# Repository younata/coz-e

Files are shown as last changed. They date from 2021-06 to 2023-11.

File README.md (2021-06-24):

# [Coz-E Build Log](https://coz-e.rachelbrindle.com)



Build log for an electric canard airplane. Built using the same technology as my [knowledge repo](https://github.com/younata/personal_knowledge).

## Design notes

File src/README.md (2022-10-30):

# Introduction - The Coz-E

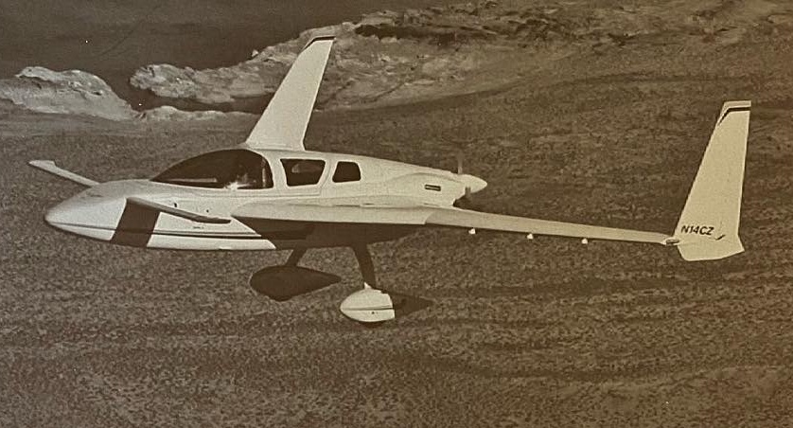
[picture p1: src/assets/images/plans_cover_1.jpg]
Image of the the Cozy Mk IV prototype, from the cover for my copy of the Cozy Plans


This is the build log (and other relevant information) for my cozy-derived electric canard airplane.

You can think of this as a [Cozy Mark IV](https://en.wikipedia.org/wiki/Cozy_MK_IV) with the rear seats replaced with a large battery compartment and an electric motor. Because that's what it will be.

Unlike [my digital garden](https://knowledge.rachelbrindle.com), which provides more generic knowledge and things I've gathered, this site is intended to scope down to the Coz-E.

## Using this site

Pages are organized on the sidebar to the left. It's sorted alphabetically, and most top-level sections have nested subsections. Sections with the chevron next to them can be expanded to show additional subsections. You can also search for things by clicking or tapping on the search icon in the top left.

There is an [rss feed to track updated articles here](/atom.xml). You can also paste any article's URL into your rss reader and it should discover the feed.

## Recent Work

The pages that I've recently been working on.

{{#recently_updated}}

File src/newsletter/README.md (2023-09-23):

# Cozy Newsletter

Marc Zeitlin has <a href="http://www.cozybuilders.org/newsletters/" data-proofer-ignore>all of the Cozy Newsletters available at cozybuilders.org</a>. Here's some of the more relevant information to the Coz-E build.

Note for builders of gas-powered Cozys: I have not included any of the tips related to the fuel and engine systems. This will be a fully-electric airplane, and so I have no reason to include those for my reference.

## Builder Tips

In addition to some of the dedicated articles going in more depth on specific advice, here's a sorted list of most of the advice given in the Cozy Newsletter.

### General

- Keep joints tight with "no joggles" to improve performance. (Cozy Newsletter \#4)
- Do not cut up the large-size drawings. Instead, trace templates onto another sheet of paper and save the original drawings intact. (Cozy Newsletter \#12) (Personally, I take photos of the drawings with a ruler for scale, but that's for archival purposes).
- "NEVER allow yourself to be distracted while working on your airplane, such that you might not complete a task, and then forget to finish it later. We all have had the experience of visitors dropping in while we are working. Even if you have to be rude, finish the job before laying down your tools." (Cozy Newsletter \#24, The Canard Pusher \#57)
- Joints between all permanently installed parts should be taped. (Cozy Newsletter \#24)
- This one comes up in more than a few newsletters: Check your attach bolts. If more than 2 threads extend through the nut, add another washer. Don't let the threads bottom out before the bolts are tight. (Cozy Newsletter \#34)
- Holes through bulkheads or instrument panel do not need to be glassed. (Cozy Newsletter \#36)
- Wherever possible, orient bolts either heads up or heads forward. (Cozy Newsletter \#38)
- "Extruded piano hinges MS20001-P6, P5, P4, etc. are all identical except for the width of the flange. It is easier just to order and stock the P6, and if the flange is wider than necessary, trim it on your band saw."" (Cozy Newsletter \#39)
- Try using a light inside to identify holes that have been glassed over. (Eric Westland, Cozy Newsletter \#39)
- For bending aluminum, rule of thumb is that the bend radius should be no less than the thickness of the material. E.G. 1/16 inch thick aluminum can bend 90°, provided the radius is 1/16 inch or greater. Always bend aluminum across the grain, not with it. (Ray Goldsmith, Cozy Newsletter \#39)
- Always order a little extra material, especially in the beginning, so that you don't run out of epoxy, cloth, micro, or flox before finishing a job. (Cozy Newsletter \#69)
- "all aluminum parts [should] be protected from corrosion by cleaning first with Alumiprep 33 or metal prep \#79, and then soaking in Alodine 1201, which is a visible (golden brown) moisture barrier, greatly increasing resistance to corrosion. This also acts as an excellent surface to bond epoxy or paint. Even if you do not live near the coast, the airplane you are building could some day end up there." (Cozy Newsletter \#81)

### Safety

- Use nitrile gloves for your hand, with water-soluble barrier cream on the arms. Switch out the barrier cream early and often. (Cozy Newsletter \#89)
  - This has evolved significantly, from the original advice, starting way back in \#7: To protect your skin from epoxy, Nat heavily recommends water-soluble barrier creams. If you must use gloves, use nitrile gloves. Under no circumstances, use latex gloves.

### Tools & Shop

- Store and dispense glass cloth on a rack in a wall cabinet. Hinge the front of the cabinet so that it opens to form a table to lay out the cloth for cutting. Keep a clean pair of scissors there just for cutting clean cloth. (Cozy Newsletter \#14)
- Put a 2 inch overhang all around your work table. This makes clamping parts to the table much easier. (Cozy Newsletter \#17)

> Neil Clayton says the tool (s) he uses the most are sanding sticks he made himself. He says Home Depot paint dept gives away 2 sizes of paint stirrers; a 1"wide stick and a 2” wide version. Both have a nicely formed handle. I always grab a handful as I pass towards the check out. Then at Lowe’s I pick up some 12” x 18” sanding sheets (the kind used on those big floor sanders). Several grades are available. I use left over epoxy to glue the stirrers to the sheets and then split them into individual sanding tools with a razor blade when the epoxy has dried. One sheet yields about 10-15 sanding sticks of various sizes so they are cheap and disposable. Try it!

(Cozy Newsletter \#78)

- Get a Fein tool for trimming cured layups and electric scissors for cutting cloth and peel ply (and trimming wet layups) (Cozy Newsletter \#82)

### Antennae

- Make sure the nav antenna misses the area in the bottom of the fuselage that will be cut out later for the nosewheel well. (Eric Westland, Cozy Newsletter \#39)

#### Location

From Cozy Newsletter \#34, with a discussion on where to place the antennas (For a Cozy 3).

- Transponder: In the nose ahead of the rudder pedals with the probe extending through a 1/4" hole in the bottom of the fuselage.
- Nav: Two good locations:
  1. Underneath the skin on the bottom of the canard, legs extending forward and offset to the radio side.
  2. Under the skin on the bottom of the fuselage, legs extending forward on either side of wheel well.
- ADF: Use King electronic antenna and locate inside cockpit under right front seat.
- Com: Located under skin of winglets, per plans.
- FM and/or Marker Beacon: Under skin mid-wing.

GPS was not specifically called out, presumably because it wasn't available back then.

- Be careful in laying out VOR antennas on the bottom of the fuselage to avoid future cut outs for the landing light and nose wheel. (Thomas Kennedy, Cozy Newsletter \#55)

> Here are the dimensions (each arm) Jim Weir has published for the following di-pole antennas:
> - Marker Beacon - 34.3 in.
> - FM Music Radio - 26.2 in.
> - VOR/LOC - 22.8 in.
> - VHF/COM - 20.3 in.
> - Amateur 2m - 17.7 in.
> - Glideslope - 7.5 in.
>
> The COM is the only one that needs to be vertically oriented. All the rest should be horizontal. The VOR should be a V shape. Some say the marker beacon should be along the airplane centerline. I installed mine in the wing and it worked just fine. You should keep the tips of di-pole antennas away from metal, and away from each other, particularly transmitting antennas. I have used Jim's measurements and they work well-better than most factory antennas. My GPS antenna is mounted in the nose, just under the inspection cover (pointed upward toward the satellites) and works well there. I like this location because the co-ax is very short. My transponder antenna is in the bottom of the nose, with the probe just sticking through the skin (pointed down toward the ground stations). You can make your own transponder antenna. It should be 2.65 inches long from the tip of the probe to the ground plane, and insulated from the ground plane. The ground plane can be made from .062 aluminum. It is about 8 inches in diameter (I lost my drawing). I have made my own from one of Jim's kits, and also from scratch, and they work well. You attach the center conductor to the radiating rod, and the co-ax ground to the ground plane. You get a lot of satisfaction when you make your own antennas, they are all hidden, and they work better than the ones that cost mucho bucks!

(Cozy Newsletter \#73)

### Canard

> Several Mark IV builders have advised us that their canards are slightly longer in cross section (chord) then shown on M-11, and when the lift tabs are in contact with the forward face of F-22, the trailing edge of the canard is 1/8 to 1/4" aft of the forward face of F-28, and that the alignment tabs cannot be built as shown. Should this also be the case with your canard, you may lay up additional plies of BID locally on the forward face of F-22 up to 1/8" thick, or remove up to 1/8" of the trailing edge of the canard locally at the tabs, or a combination of both.

(Cozy Newsletter \#44)

> Canard installation. Make sure you allow for at least 3/4" of horizontal travel for the canard so the incidence pins will not bind during installation or removal.

(Cozy Newsletter \#50)

> Some builders are still having trouble with the trailing edge of their canard being too low, such that the airfoil dips down and they have to mount the elevators lower than desired to get the required 15 degrees of trailing edge up travel. We suggest that you remove 1/16th inch (no more) from underneath the fishtail on the templates before cutting the foam cores, or from the foam after cutting to avoid this problem. We have made this suggestion to Feather Lite as well to do on their precut cores.

(Cozy Newsletter \#53)

### Canopy

On getting a smooth edge where the fiberglass contacts the canopy:

> Builder Wayne Hicks said he made a paper pattern of the canopy deck, then laid up the 2 UND on plastic (and later the 2 BID), used the pattern and razor pizza cutter to make a nice, clean cut along the pattern lines. Then he laid the piece nice and neat up against the glass. There were absolutely no problems. No excess flox, no excess resin, no excess glass. Never had to use a dremel! If anything, all he had to do was cut one or two stray strands with a razor blade. He did this for both the outside and inside canopy deck layups, and highly recommends this technique.

(Wayne Hicks, Cozy Newsletter \#70)

> to avoid corrosion of the canopy hinge attach bolts. Saturate the bare wood in the holes through the longeron with epoxy to seal the wood fibers. Do this by dipping a cotton swab into epoxy and then inserting it into the hole. Alternatively, you can drill the hole slightly oversize, fill it with flox, and after cure, redrill it to the correct size.

(Nick Parkyn, Cozy Newsletter \#83)

### Contouring

- Fill low spots before sanding surrounding areas down to contour. This keeps your low spots from turning into high spots. (Cozy Newsletter \#22)

> I found a method to make the final canard contour perfect per plans. I used the checking contour templates for the canard to cut out (hot wire) a block of styrofoam. Then I stuck a large piece of sandpaper to it and used it to give the canard a perfect contour over its entire length. The same thing worked fine for the elevators.

(Jean-Jacques Claus, Cozy Newsletter \#85)

### Cowlings

> Cowlings should have extra layers of BID along all the edges to make them more rigid when they are removed from the airplane, and to provide more beef for the fasteners. This is shown in Figures 12 & 15, Chapter 23, but builders were not instructed to add them because the supplier (Featherlite) added them while the cowlings were still in the mold. In February 1999, when we inspected AeroCad cowlings, we noticed that they were not doing this. We asked them to add the extra layers while the cowlings were still in the mold. They agreed, and we approved their cowlings contingent upon their doing this.

(Cozy Newsletter \#68)

### Elevators

> Your elevators should balance with the weights shown in the plans. If they do not, do not try to balance them by adding weight inboard. Instead, discard them and make new ones more carefully to make them lighter (you can probably re-use the torque tubes and other hardware). The mass balance called out for the elevator and the specification for balancing them applies only to an elevator fabricated with the same weight and stiffness as that which has successfully passed all the flutter testing. It is extremely important, and life-critical that the manufacturer or owner of each Cozy, or any plane for that matter, assure himself without a doubt, that the control surfaces are conformal to those which have passed flight tests and been shown to be flutter-free.

(Cozy Newsletter \#24)

> Elevator torque tube offsets (CZNC-12A for the Roncz canard). The drawing we submitted to Brock Mfg. stated that these offsets should be a slip-fit in the l" OD x .035" 2024 T3 torque tube. Brock Mfg. cannot guarantee a slip-fit because the tolerance on wall thickness for .035" 2024 T3 drawn tubing is +/-10 %. To prevent too loose a fit if the wall thickness is on the thin side, the specification for the offsets has been tightened to .930' OD. If the wall is on the thick side, you will have to sand the offsets to obtain it slip-fit.

(Cozy Newsletter \#50)

> In the first edition Mark IV plans Chapter 11, p.7, we instructed builders to mount their elevators at zero degrees with jig L so that there was a .2 inch gap between the canard and the elevator. When some builders did this, they were not able to get 15 degrees trailing edge up of the elevators. So we changed the L jig (see p. M-18) to mount the elevators at 15 degrees trailing edge up and zero gap. Please note this on p. 7, Chapter 11, 1st paragraph and Figs. 17 & 18.

(Cozy Newsletter \#68)

### Epoxy

Starting with Cozy Newsletter \#61, the MGS system is now recommended. Either the L335 or L285 system.

- Save the foam scraps. Many parts can be made by gluing small pieces together with 5-minute epoxy. (Cozy Newsletter \#5)
- To conserve epoxy, mix microballoons with any excess into a very thick paste, and trowel that over your finished fiberglass parts. This will save you time when finishing. Rough the surface with 36 grit sandpaper first, though. (Cozy Newsletter \#5)
- Lava soap works great to remove epoxy from your hands. (Cozy Newsletter \#35)
- Use the bottom of 8 ounce mixing cups to make 5 minute epoxy (Cozy Newsletter \#17)
- Store near-empty bottles of 5 minute epoxy on their side. (Cozy Newsletter \#28)
- Mixing some flox with 5 minute epoxy will make a bit stronger joint and prevent it from running. (Cozy Newsletter \#35)
- Epoxy Resin should be clear and colorless (or a slight yellow). Hazy indicates crystallization, and the epoxy should not be used until it is heated and becomes clear again. (Cozy Newsletter \#85)

> Cozy builder Phillip Johnson, in the Pacific Northwest, protects his resin and hardener from exposure to air by putting a plastic bag over the top of his plastic containers in his dispenser after filling them, with the bag resting on top of the liquid surface and with enough slack so the bag will follow the surface down as material is used, and then putting the cover on the container.

Cozy Newsletter \#54

### Fiberglassing

- Micro joints (which hold urethane blocks together) cause bumps when glass is laid over them. Undercut all joints with a dremel before shaping and before layup. Fill the undercuts with fresh micro just before the layup. (Cozy Newsletter \#5)
- To prevent air bubbles from coming back in after being worked out, cover the cure area with saran wrap (or any plastic wrap) and squeegee the air out. (Cozy Newsletter \#5)
- Cut the glass cloth ahead of the layup to the approximate size. Do this after the foam is vacuumed, but before applying any epoxy. Drape the cloth over the part, cut it to size, label it with a felt-tipped pen, roll it up and set it aside. (Cozy Newsletter \#14)
- To prevent UNI from unraveling when cutting it lengthwise, lay down a strip of masking tape and cut down the tape's center. Scissor trim the masking tape off after the cloth has been wet in place. (Cozy Newsletter \#14)
- Use a sabre saw, not a band saw, to cut fiberglass. (Cozy Newsletter \#17)
- Use a rubber squeegee to spread epoxy on the glass. Take a 6 inch squeegee, and cut it in 2. Remove the epoxy after use. You can use a belt sander to remove any cured epoxy, but it's less work to just clean it. (Cozy Newsletter \#31)
  - It takes a couple of minutes for epoxy to soak in and wet out one or two layers of glass cloth. Rather than waiting for this to happen in a small area, use this time to spread epoxy over as wide an area as possible. Pour a ribbon of epoxy on the cloth and follow behind with the squeegee spreading it. Keep the pressure very light, so as to not disturb the cloth. After the cloth is wet out, you can increase the pressure of the squeegee to distribute it. You can pick up excess epoxy with your squeegee, wiping it off on the edge of your mixing cup. Conversely, you can apply a small amount of epoxy by dipping your squeegee into the mixing cup. If you practice these techniques, you will find that you can make lay ups much more quickly.
  - Do not waste time trying to get just the right amount of epoxy on the lower layers of a multi-ply layup. Actually, cloth wets out better from underneath and not as much air is trapped between layers. It is only on the last layer that you need to spend the time working on getting the air out an applying the optimum amount of epoxy.
  - Do not leave bristles from the throw-away brushes behind in your layups--they weaken it. You can pick them up with the tip of a brush.
- Double check that you remove the peel ply. If you leave it in and glass over it, the part must be discarded and rebuilt. (Cozy Newsletter \#37)
- Instead of peel ply tape, get the 38 inch wide peel ply. Then, when you need tape, cut the peel ply to whatever width you need. (Eric Westland, Cozy Newsletter \#39)
- "Buy cheap 100% polyester (or Nylon) cloth (peel ply) by the bolt and cover all layups with it. First test a sample piece to make sure no additives are present that may cause removal to be difficult. I find that I do not need to add extra resin to wet out the polyester, just stipple and use a hair dryer. I make it a habit to strip the polyester the next day, so none is left by mistake. This eliminates the need for a lot of sanding, and dust breathing. All layups look and feel smoother." (Steve Blank, Cozy Newsletter \#46)
- "We use peel ply extensively on all of our layups. Glass fibers act somewhat like a sponge, and can soak up extra resin. If a layup is resin-rich, it is not only too heavy, but it is weaker than a layup with just the right amount of resin. The peel ply seems to hold the fibers down more compactly, so they don't soak up too much resin. Sort of a poor man's vacuum bagging. If you use peel ply, you can make the layup a little wet, then lay down the peel ply, and with a squeegee and hair dryer, remove the excess epoxy (if the layup was really wet) or else free up almost enough epoxy to wet out the peel ply, and add epoxy as necessary to wet it out completely. The only thing you need to be careful of is that the layup underneath the peel ply isn't so dry that it is porous, because then the compressive strength would suffer (buckling in compression). Synthetic fabrics with a straight weave (not knit), like nylon, polyester, or dacron, as long as they aren't fuzzy, and don't contain cotton or rayon, seem to work well. Sometimes you can find real bargains at fabric stores. But test a swatch first. Alexander Aeroplane lists peel ply at $2.25/yd. in 45" widths, which is quite reasonable." (Cozy Newsletter \#47)
- "BID is always cut on the bias and overlapped l' in every direction, but UND is overlapped only in the direction of the major fibers." (Cozy Newsletter \#50)
- Whenever possible, use peel ply. As an extra precaution, sand the surface that the peel ply was on before applying the bond. (Cozy Newsletter \#55)
- A wet-on-wet layup usually results in the strongest bond between layers. To do this, wet out the first layer of glass, squeegee the air out, but leave an excess of epoxy and then lay down the next layer of cloth on top to soak up the excess. (Cozy Newsletter \#55)
- Do not glass over a cured, microed surface, if structural strength is required. (Cozy Newsletter \#55)
- Put flox in a bag and dispense it like cake frosting. (Dave West, Cozy Newsletter \#62)
- In tight corners where it's hard to roughen up the surface with conventional sandpaper, try a carbide studded grout removal tool that has carbide deposited on the edge of a steel blade approx. 1" long attached to a handle with a slight "S" bent arm. (John Fritz, Cozy Newsletter \#66)

> Early in the game we learned that various fabrics sold in fabric stores work well as peel ply, and can sometimes be purchased at quite a low price. We learned that hard-weave (not fuzzy or stretch weaves) nylon, polyester and dacron work well. Watch out for cotton and rayon. Often there are roll ends tables where things are reduced for clearance. Once I was able to purchase nylon like is used in ski jackets for $.45/yd, and later wished I had bought the entire table. It is best to take a sample home first, use it on a wet layup, and make sure it peels off, before buying a whole bunch. Make sure you iron any wrinkles out of peel ply before using it. Otherwise they transfer to the layup.

(Cozy Newsletter \#68)

- A general rule is that whenever joining two or more intersecting surfaces together, they should always be floxed and taped, whether instructed to do so or not. (Cozy Newsletter \#71)

- - A rule of thumb for estimating how much mixed epoxy you will need for any given layup is 1 oz of epoxy for every oz of cloth needed. This includes the micro layer. "For example, the bottom side of one Cozy MKIV wing will need 12 yards UNI (7 oz/yd. 38” width) or 84 oz. total. Epoxy weighs 9 lbs. (144 oz) per mixed gallon, so you will need 84 oz. mixed epoxy to wet out 12 yards of UNI." (Cozy Newsletter \#80)
- Leave a little mixture of epoxy in the cup and check it for cure the following day. If it has cured correctly, a scratch on the surface will leave a white mark (Cozy Newsletter \#81)
- "[If] glass cloth wets out and becomes transparent, it is safe to use. If it stays white, throw it away." (Gary Hunter, Cozy Newsletter \#83)
- "DO NOT USE glass that has become wet." (Gary Hunter, Cozy Newsletter \#83)
- Take your time. Do not apply epoxy until you are 100% satisfied with the shape and integrity of the part. (Neal Johnson, Cozy Newsletter \#84)

#### Tom McNeilly's Vacuum-bagging technique

From the Cozy Newsletter \#4, this describes a way to get very light layups using vacuum bagging. Later newsletters state that vacuum-bagging is generally not worth the effort, though.

> Place the layup down as quickly as you can, cover it with perforated poly. Cover that with soft carpet underlayment foam, and cover that with regular poly. Tape down the edges, and pull a vacuum with a vacuum cleaner house between the layers. The vacuum should squeeze the excess epoxy out of the layup and into the soft foam. After cure, strip the coverings off, including epoxy. Tom claims this saved 6 lbs per wing.

#### Dealing with BID

- You can create 2 inch wide BID cloth tape by rolling the BID cloth into 1 inch diameter rolls at 45° to the selvage edge. (Cozy Newsletter \#4)
- For installing BID into the corner tapes: Layup the BID you'll need onto the foil. Squeegee it out to a good layup. Cut your tapes out of this layup, cutting through the glass and aluminum foil. Sand and paint a coat of epoxy onto the area to be laid up over, then use your fingers to bend the aluminum foil to form the tape into an angle to fit into the corner. Position it, then lightly squeegee or stipple it into place. Peel the aluminum foil off, stipple any remaining air bubbles out, peel ply the edges. (Cozy Newsletter \#4)
- Sand a slight recess (1/32 inch) into the foam on flat or curved surfaces where you'll place BID overlap joints so overlaps won't cause a bump in the finished surface. (Cozy Newsletter \#5)

### Finishing

- Don't use featherfill. It does not bond well with epoxy and will cause the paint job to delaminate in a year or two. (Cozy Newsletter \#10)
- Make sure to fill and finish paint the inside of the cowlings. (Cozy Newsletter \#22)
- Most silicones give off corrosive fumes, Dow Corning Silastic RTV 738 is a non-corrosive sealant, use it to secure the cover plates over the wing attach bolts. (Bruce Ibbotson, Cozy Newsletter \#22)
- Use Polyurethanes, not Enamels or Lacquers. Enamels and lacquers chip in heavy rain. (Vance Atkinson, Cozy Newsletter \#23)
- "It is not necessary to use a spray booth to paint an airplane and get a good finish. You can spray the finish coat in a garage or outside. After cure, wet sand with 1000 and then 1500 grit, and then buff with 3M Finess-it II. This will remove orange peel, overspray, dust, and other imperfections and result in a very flat surface with high sheen. This works well with Ditzler Deltron (acrylic urethane) which is the finish we recommend." (Cozy Newsletter \#41)
- "We recommend use of a high-build epoxy primer. Cozy builder Nick Parkyn in Western Australia says that he has used the new System Three water reducible Epoxy Primer and
Polyurethane paints and is impressed with the performance. We are not familiar with these products and have asked him for more information. We would welcome other builders input." (Cozy Newsletter \#41)
- "Have you ever tried to pour paint from a full 1 gallon can and had it run down the side? Try this. Wrap a strip of masking tape (2- wide works the best) around the top of the can, and punch a hole in the groove around the rim. You should be able to pour without spilling, and the excess paint should drain through the hole back into the can. The hole will be sealed after the cover is reinstalled." (Cozy Newsletter \#41)

> Mark IV builder Chuck Larson writes, "I've discovered a tip that works great for wet sanding the Sterling primer. I use a grouting trowel which is used for grouting ceramic tile. I bought mine years ago at Color Tile. It is 9" x 4". It has a wooden handle attached to an aluminum plate which has dense rubber foam bonded to it. Wet or dry sandpaper will adhere to the foam rubber well enough to allow the sanding. It keeps the surface flat, and it is easy to remove and wash out the sandpaper".

(Cozy Newsletter \#44)

> If you need to pour paint from a can without spilling and wasting a lot (paint is expensive!), first punch a hole in the trough around the rim to let paint drain back into the can. Then wrap some 2" tape around the rim of the can, extending up above the rim about 1-1/2". Now you can pour the paint out of the can without it running down the side of the can, and any excess will drain back into the can.

(Cozy Newsletter \#45)

- If you use masking tape when painting, don't leave it on a long time, and when you remove it, pull it back at 180° to itself, not 90°. (Cozy Newsletter \#63)

>
I just completed painting the bottom of my plane. I've used the new poly fiber system. All water based. Very impressed. Pin holes are a total non-issue. Particularly when you use the Superfil instead of normal microballoons. Superfil is substantially better than micro. Trapped voids are rare. Sands easy, mixes easy. Areas where I used micro have more pinholes, but using the Smoothprime primer is highly effective at filling pinholes. It really does flow into holes. Must have low surface tension or something. I also elected to use their water based "topgloss" top coat (polyurethane). So far, I really like it, but I have yet to color sand and buff the paint, so the verdict is still out. I haven't done adhesion tests yet. On my second coat (of three) of topgloss, I got too aggressive and had quite a few runs on corner radius. I elected to sand the entire coat before applying my last coat. Final coat looks good, although areas have a matte appearance (too lean). No runs. The top coat appearance is quite sensitive to spray quantity. More is better unless you develop runs. I had no problems with vertical surfaces. I learned that I don't need to use finer than 120 grit when sanding micro or superfil. The primer fills all those scratches fully. I used a sanding stick only to achieve straightness, then I used an electric random orbit sander with 220 grit. I was willing to sand the primer completely off to achieve uniform appearance. I mixed paint and primers 1 cup at a time to avoid splatter. I've heard people describe sanding and painting as the worst part of the process, but I enjoy it. It's great to see objects finally transformed into airplane like appearance. Just wanted you to know more about these new products. My superficial conclusions: Superfil micro replacement is way better. Smoothprime primer is way better. Topgloss top coat may not be better (lotta work)....we'll see when I'm further along.

(Al Wick, Cozy Newsletter \#67)

> I put the drip lip on the front fuselage cover last night. Here is a hint for those who have yet to do this. The plans say to build up an 1/8 inch ledge with balsa or foam. I used a piece of 1" wide webbing (either climbing rope type webbing or load binding strap type webbing) with duct tape on top of it. The webbing will bend around the curve just right, and it is about the right size.

(Norm Muzzy, Cozy Newsletter \#72)

- Do not use polyurethane paint. Nat recommends a acrylic-urethane (PPG "Deltron" or "Concept") (Cozy Newsletter \#83)

### Fuselage

- If you have difficulty stickling the copper foil tape to the bottom of the fuselage, try heating it with a hair dryer and pressing down on it with a hard rubber roller. (Eric Westland, Cozy Newsletter \#39)

#### Fuselage Sides

- Put a 6" wide strip of wax paper between the masonite and the foam pieces where the edges butt together. This will make the eventual removal from the jigs MUCH easier. (Thomas Kennedy, Cozy Newsletter \#49)
- In assembling the bulkheads to the sides, forget the ropes to tighten the whole assembly. Use threaded rods and wing much more precise control. (Thomas Kennedy, Cozy Newsletter \#49)
- Buy a kiln-dried board (not construction grade) for your WL 0.0, and use bolts rather than nails to secure. This will allow precise placement and later shimming if required. (Thomas Kennedy, Cozy Newsletter \#49)
- I had very good results mounting my WL 0.0 board on my work table which was mounted to 4x4s glued to my garage floor. There is no such thing as a level garage floor. The work table becomes your level surface. (Thomas Kennedy, Cozy Newsletter \#49)

### Foam

- Before cutting wing sections, clamp the styrofoam blocks and glue them using pour foam. This produces very thin joints that keep the styrofoam joined together while still allowing the hot wire to cut them without catching. (Tom McNeilly, Cozy Newsletter \#4)
- You can use a dremel tool with a router attachment to make the small depressions in foam as called out in the plans. (Cozy Newsletter \#15)
- Covering the edges of hot wire templates with copper foil tape makes them easier to use (Cozy Newsletter \#38)
- "The 2 lb./cu.ft. large cell blue styrofoam called for in the plans is called Styrofoam in the Aircraft Spruce catalog, Polystyrene in the Wicks catalog, and extruded Polystyrene in the Alexander catalog. Urethane foam may also be called Polyurethane foam." (Cozy Newsletter \#39)
- Use a router to carve 1/8 inch and 1/16 inch relief cuts in the foam (e.g. in chapter 9, on the landing brake). Attach the router base to a 36 inch long board to make quick, smooth work of the cuts. (Eric Westland, Cozy Newsletter \#39)
- Try using double-sided tape on the forms to hold the foam down. Recommended the kind used on golf club grips or carpet tape. Should peel right off with little or no effect on the foam. (Mark Loy, Cozy Newsletter \#64)

> If you “screw-up” when cutting airfoils, and have a bad cut on one side (top or bottom), no need to throw it away and start over. Just slice the airfoil apart, and splice in a piece of styrofoam (like making a sandwich), and re-cut it. Don’t know how to make a sheet of styrofoam? Just clamp your hotwire saw 1⁄2 inch or so above your work bench, and slide your scrap chunks of styrofoam underneath, sorta like cutting boards from logs. The beauty of composite construction is its hard to spoil something so bad you can’t fix it.

(Cozy Newsletter \#77)

### Joints

> For Structural reasons, all joints should be taped with 2 plies of BID 2' wide (1" on each surface) cut on the bias (45 degrees) unless otherwise specified. After application, the tape should be peel-plied. One recommended way to accomplish this is to wet out 2 plies of BID on wax paper or Saran wrap, cut into strips, apply over joints, remove the wax paper or Saran wrap, cover with peel ply and wet out same. Wax paper should only be used with discretion. It should not be left in place while the epoxy cures, because wax will be left behind, and it should only be used on those joints which will not be later covered with additional layups.

(Cozy Newsletter \#50)

### Landing Gear

- "If you wrap the gear leg first with 1/8" fiberfrax, and then with shiny aluminum, you will greatly reduce the heating by radiation." (Cozy Newsletter \#24)
- "Provide a vent for hot air to escape from your wheel pants. Hot air rises and will be trapped inside the wheel pants unless you provide a vent, on the top, on the disc side, for it to escape." (Cozy Newsletter \#24)

> In Chapter 9, p.2, it says that the [landing gear] strut should be cut at 8 degrees, but on p.3 it says 13 degrees. There has been some disagreement as to what is the correct angle, and it also depends on whether it is measured at the leading edge or trailing edge. The angle is not critical, so shoot for somewhere in between.

(Cozy Newsletter \#68)

> I thought it was in the plans, but maybe not. An easy way to make the fairing where the main gear strut enters the fuselage is to shape it with molding clay (Playdough), glass over with at least 2 layers of BID, attaching to both the strut and the fuselage. Then after cure, make a saw cut at least 1/8" wide halfway between the fuselage and strut, remove the strut, and dig out the clay. If the cut is wide enough and the inside of the fairing is empty, the strut can flex without cracking the fairing. This should be done when the fuselage is upside down with no weight on the gear. Then when you are flying, both halves of the fairing will be aligned for minimum drag.

(Cozy Newsletter \#72)

### Panel

- Don't cut holes for your panel until everything else is done, and you've put together the instrumentation. Build a mock panel first (Nat suggested 1/4 inch plywood. You can also use cardboard) to test it out. (Cozy Newsletter \#5)

### Spars

> The 3 inch spar cap material presently being supplied is only 2-3/4 inches wide, but not to worry. If you pull out the cross threads as instructed for the canard, centerspar, and wings, and then squeegee after applying epoxy, the strands spread out to 3 inches, and you will be able to fill up the troughs with the maximum amount of glass they can hold.

(Cozy Newsletter \#65)

### Strakes

> Bending 3/8 in. PVC is a universal problem. When I re-built my right strake, I made a scribing tool from a block of wood and a hacksaw blade. I made a saw cut in the wood and 5-minuted in the hacksaw blade so it protruded 1/4 in. I carefully scribed a number of cuts in the PVC where I wanted it to bend, then bent it into the frame and fastened it in the bent shape, and then microed and glassed the scribed surface. That worked better than anything else I have tried to date.

(Cozy Newsletter \#10)

- Postpone installing the center section spar and building the strakes until you have completed as much work inside the fuselage as possible. It is much easier to work inside the fuselage with it sitting on its side on saw horses. (Cozy Newsletter \#35)

> It is important for appearance that the strakes are straight (no bumps), and properly aligned with the wing. The wing should be installed on the center section spar when the strake is built, and a straight edge should be used to make sure that the leading edges of the ribs are aligned with the leading edge of the wing, and that all points on the rib airfoils align with the wing airfoil. Of course, you will need to make allowance (using spacers) for the 3/8" foam and several layers of glass skin which will be subsequently be laid over the ribs.

(Cozy Newsletter \#44)

> Strakes, Chapter 21, p.2. Please note that the fuel cell ends at Rib R-57. The empty space outboard is necessary as a buffer to prevent any fuel, liquid or vapors, from reaching the wing. An open drain at the low point would indicate any fuel leakage through R-57.

(Cozy Newsletter \#64)

> Keith Scull (England) didn't want to pay the cost of shipping Featherlite's leading edges all the way from California, and he didn't like the idea of carving foam blocks, so he came up with an innovative alternative. He purchased some thin card stock from a local art supply store, wrapped it around the leading edge of the strake using the ribs as guides, trimmed it so it just fit into the recess provided for the leading edge layup, and taped it in place with 20 inch long strips of masking tape. Then he cut openings in the top so he could pour pour-foam into the empty space. The openings were 3 in. x 1/2 in. every 6 to 9 inches parallel to the strake leading edge. He poured the pour foam thru the slots, let it expand and cure, and then removed the masking tape and card stock. He said the result was a perfectly formed leading edge which required very little sanding to prepare if for the glass layup (see pictures). He said it sounds like a lot of work, but only took a couple of hours, and did a better job with less mess.

> Keith said when he leak tested his strakes using an altimeter, the right strake had a very small leak (20 ft. in 3 hrs.). He couldn't find it with soapy water. So he called in a local refrigeration man who filled the strake with R22 and used an electronic sniffer to locate the escaping gas. He found the leak. It was traveling along the score lines he had cut in the foam to bend it around the ribs, and escaping where the foam joined the fuselage. Apparently he hadn't completely filled up these score lines with micro. The cure was quite simple. He drilled a very small hole thru the top skin into the score line at the tank rib and injected epoxy using the vacuum method described in the plans. To be doubly sure, he did this with every one of the score marks, and found three to be leaking. After filling with epoxy, the altimeter indicated no more leaks.

(Cozy Newsletter \#68)

### Wings

> There is a discontinuity (dip) in the top surface of the wing at B.L. 67.5 (see Chap. 19, p. 10). This is intentional. You have not made a mistake!

(Cozy Newsletter \#53)

> when you attach the wings many times in the shop, don't use the
AN365 nuts over and over again, but instead get some fine thread nuts at the hardware store which are much easier to install and you don't have to worry about them wearing out.

(John Epplin, Cozy Newsletter \#73)

### Unsorted

#### Jim White's advice

From Cozy Newsletter \#67, copied verbatim:

1. Attach the wing before working on the stake and bondo a 1/4" or so thick template to the end of the main spar that matches the contour of the wing. This is needed so that the strake matches up to the leading edge.
2. When cutting out the top and bottom PVC foam pieces, finish one (top or bottom). The top is the same as the bottom except it is 0.2" longer. All the angles are the same. Use the top or bottom strake as a template by simply shifting it up or down 0.2" accordingly. You might as well make all four top and bottom skins at once. GET THE FIRST ON RIGHT, OR YOU WILL HAVE 4 WRONG ONES.
3. I placed blocks under the ends of the landing gear struts to level the airplane perfectly and give it a solid foundation. I supported the jig table with two saw horses, and four pieces of 2x4's individually clamped to the saw horses. The jig table simply rests on the ends of the 2x4's that are adjusted up or down.
4. INSTALL THE RELEASE TAPE ON THE BACK OF THE JIG TABLE BEFORE ATTACHING IT TO THE MAIN SPAR.
5. Use long clamps from the top of the spar to the jig table beneath to firmly attach the plane to the jig table, inboard and outboard on the spar. I did not use any bondo and the jig table never moved relative to the plane, even when getting in and out of it repeatedly to cut out the openings and tape the inside joints.
6. I believe the strainer inspection hole in B33 is marked wrong in the plans. The inspection hole should start 6" from the spar, not 3".
7. For B33 bulkhead reference I clamped a straight edge to the canard bulkhead and strung a string back to a mark on the top of the spar. For the B57 bulkhead I simply used a plumb bob hung over the edge of the jig table at BL 57 and attached the other end to a mark at 57" from centerline on the spar.
8. The B.L. dimensions are to the INBOARD face of the bulkhead. Carve the outboard to get the contours of the bulkheads to match the sweep of the strake. DO NOT CARVE THE INSIDE EDGES.
9. String a line from the leading edge of the template you made in step 1 above to the fuselage using the leading edge of the bulkheads as a guide. This will ensure the leading edges of the wing and strake come together.
10. 1 inch spacing is fine for the scoring of the bottom foam to bend around the ribs.
11. On the top foam, 1/2 inch cuts minimize the flat spots which occur on the top of the
curved part of the strake between the two bulkheads. Make the cuts just after the 1 ply layup has cured. If you can make the cuts while the fiberglass is hard but still pliable, you can bend it over the ribs and let it finally cure in its final shape.
12. I fully trimmed the strake openings into the fuselage before putting the top on permanently. If you jig the top foam sufficiently, it will match up repeatedly to the same place on the fuselage.
13. I wanted to make sure my upper skin was firmly attached to the ribs so I made a flange to go on the bulkheads instead of simply stacking flox on the bulheads. The flox method probably works just fine, but I have heard of some Cozys developing fuel leaks after time and thought this might minimize the possibility of this occurring. This modification added several days work to the process! When the top foam is all ready to flox to the bulkheads, I carefully marked the location of the bulkheads on the bottom of the top strake skin. I then turned the top foam over. You only need to do this for the interior fuel tank edges. Do not extend the flanges into the storage area. You can tape those areas like normal. Do the leading edge, but not the trailing edge along the main spar. On top of each bulkhead marking I put a wide layer of box sealing tape, followed by a layer of peel ply, one layer of bid tape 2" wide, and peel ply on the outer edges of the 2" bid tape. On this second layer of peel ply, DO NOT PUT THE PEEL PLY WHERE THE BULKHEAD OR RIB WILL SIT. Err on the cautious side when putting on this peel ply. You can always sand the area not peel plied, but it is difficult to remove peel ply between the flange and bulkhead. Place a thin layer of flox on the bulkheads and place the top on to cure. Let it fully cure for at least a day or the one layer of bid will sag after you pull the top back off. Pop the top off and remove all the peel ply. Glass the interior corner of the new flange with one layer of bid tape, let cure, trim with dremel, and "voila", flanges that perfectly match your strake skin.
14. When you place the top skin to the bulkheads and ribs, realize that it is a ton of work to tape all the inside edges. But doing the top skin placement and inside tapes in one sitting will save lots of sanding while upside down in the back of your airplane.

### Owners Manual

#### Updates from Newsletter \#52

From Cozy Newsletter \#52:

Do not fly until you add the following information to the Takeoff performance section of the Owners Manual, and comply:

**High Density Altitude Takeoffs**

The combination of high aircraft gross weight and high density altitude represent significant dangers for takeoff obstacle clearance. Special care is required to avoid premature rotation, i.e., if liftoff is too slow, the aircraft will be on the back side of the power curve and may not climb.
When operating heavy and high (say, within 100 lbs. of gross weight and above 5,000' density altitude) do not fully rotate to liftoff attitude until your airspeed is within 5 kts. of the best rate of climb speed, for your specific weight and altitude (see climb charts). This will require more runway than a slower liftoff, but will assure the best capability to clear obstacles and continue a safe climb. Never attempt takeoff under conditions in which you cannot achieve best rate of climb speed while still on the available runway. If this ability is not clear at any point during takeoff_abort. Off-load weight or wait for a cooler time of day.
Lift-off is possible as slow as the minimum lift-off speed, and can be successfully used at light weights and/or low altitudes to achieve a short ground roll. However, that technique will usually result in inadequate initial climb if used when heavy or high.
Runway slope effects are minor when light or at low altitudes, but they become very significant when heavy/high. For example, a 1% uphill runway slope may add well over 1,000 feet to the distance required to clear an obstacle. Never take off uphill when your takeoff toll performance is marginal. Never continue a takeoff if crosswinds require you to brake so much that a safe liftoff is in doubt. Always use best power mixture for high altitude takeoff conditions. An over-gross weight takeoff that seems like an acceptable operation near sea level can be a real killer when hot and high. Never attempt a takeoff when over approved gross weight!

There may be considerable variance in takeoff capabilities from one homebuilt aircraft to another of the same type. Engine installed power and propeller efficiency at low speeds may be less than that for the prototype that provided the basis for the takeoff distance charts. Find a long runway and measure your takeoff capability at the weights you intend to fly. If your actual performance is less than the charts, correct the charts or improve your prop and/or engine.

#### Updates from Newsletter \#56

From Cozy Newsletter \#56.

Page 46, ENVELOPE EXPANSION: Add this:

Caution:

Before expanding your flight envelope, you should make sure your airplane has positive pitch stability; i.e., if you trim it for level flight and then either pull back on the stick or push it forward, upon release of the stick, it should return to level flight in no more than 3 oscillations.

Also, before expanding your flight envelope, you should double check that your canard is set at the right angle of incidence and/or your c.g. calculations are correct by comparing elevator position with the flight test data for our plans model shown below. If your elevator position differs by more than 1 degree, land and re-check your canard incidence using template "G", and re-check weight & balance and c.g. calculation. Do not fly until you have determined the problem and corrected it.

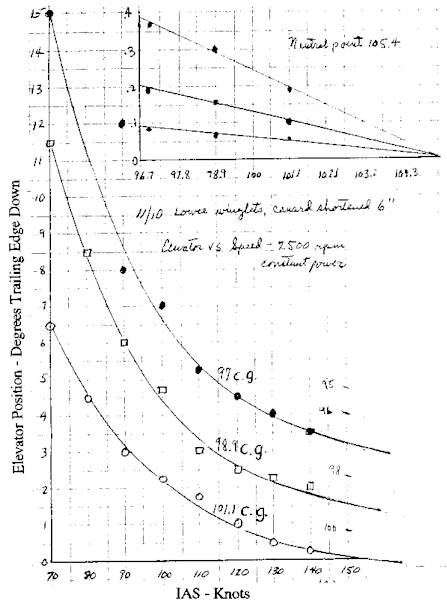
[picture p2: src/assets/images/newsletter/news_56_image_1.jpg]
Elevator position diagram


- Page 19, Stall Characteristics, 2nd para.: After "shortening the canard span 6", add "to a resultant tip to tip span of 151".
- Page 19, Stall Characteristics, 3rd para.: Instead of "plans", substitute, "1st edition plans". Page 19, Stall Characteristics, end of 3rd para.: Add, "This applies to builders with 1st edition plans. The canard span has already been reduced on 2nd edition plans to 151" tip to tip.
- Page 25, under recommended entry speed for Stalls, after "Slow deceleration" add "from level flight only".
- Page 25: Delete "Accelerated Stalls" as an approved maneuver.
- Page 33, Canard incidence: Delete "templates B & C" (a holdover from the 3-place Owners
Manual), and change to "template G".
- Page 33, Canard incidence: Change tolerance from +_ .3 deg. to + .6 deg and - .0 deg.

#### Updates from Newsletter \#64

- Page 35, Main landing gear: Check wheel camber. When aircraft is empty, wheel camber should be between 2.5 to 3.0 degrees negative (bottom of wheel tilted in). Measure after pushing aircraft forward at least 5’, then aft 5’ and take average. Record in aircraft log book.
- When checking for proper toe-in, wheel camber should increase slightly when pushing forward and decrease slightly when pushing aft.
- Page 50, Annual inspection: Check wheel camber and toe in as prescribed on page 35 and record in aircraft log book.

#### Updates from Newsletter \#65

- Page 35, Main landing gear: Check wheel camber. When aircraft is empty, wheel camber should be between 2.5 to 3.0 degrees negative (bottom of wheel tilted in). Measure after pushing aircraft forward at least 5', then aft 5' and take average. Record in aircraft log book.
- When checking for proper toe-in, wheel camber should increase slightly when pushing forward and decrease slightly when pushing aft.
- Page 50, Annual inspection: Check wheel camber and toe in as prescribed on page 35 and record in aircraft log book.

## Mark IV Part Weights

David Domeier (unfinished)

| Item | Weight (lbs) |
|---|---|
| Center Section Spar | 48 |
| Fuselage on gear (no canopy or strakes) | 242 |
| Canard & elevators | 33 |
| Right wing with winglet & aileron | 69 |
| Left wing with winglet & aileron | 68 |
| Turtle deck with glass | 12 |
|------------------------|----|
| Total | 472 |

As of Cozy Newsletter \#50, this wasn't all of the weights.

Paul Kuntz (unfinished)

| Item | Weight (lbs) |
|---|---|
| F22 Bulkhead | 2.45 |
| F28 | 10.7 oz |
| Seat back | 5 lbs, 1.9 oz |
| Lower forward landing gear bulkhead | 1.4 |
| Upper forward landing gear bulkhead | 0.7875 |
| Aft landing gear bulkhead | 2.7 |
| Lower firewall | 1 lbs, 14.5 oz|
| Center firewall | 10.2 oz |
| Upper firewall | 3 lbs, 7.8 oz |

## Flying advice

- When filing for IFR, use the designator CZ-10. (Cozy Newsletter \#36).
- Keep a fire extinguisher in the plane.
- When filing flight plans, the correct designator for the Coze 3 and 4 place aircraft is HKB (Cozy Newsletter \#43)
- As of Cozy Newsletter \#51, use COZY as the designator when filing flight plans.

### Flight Testing

- One of the tips in Cozy Newsletter \#51 suggests AC-90-89A, Amateur-Built Aircraft and Ultralight Flight Testing Handbook. The current version is [AC-90-89B](https://www.faa.gov/regulations_policies/advisory_circulars/index.cfm/go/document.information/documentID/1027429)

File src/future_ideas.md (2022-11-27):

# Mods to Investigate After Flight Testing Phase 1

The goal of the initial build is to get a safe, flying airplane as soon as possible. These are ideas for modifications that I want to do which are antithetical to that goal - they're either experimental even for a homebuilt (and thus will take time to investigate and get right), or are ridiculous/a level of extra that I don't need yet.

I also want to get these out of my head so that I can stop thinking about them when I should be thinking about/working on/doing research for the main build.

## Carbon Fiber Canard, Wings, Strakes and Winglets

Just shy of making an entirely new airplane is replacing most of the exterior with carbon fiber parts. This would almost certainly result in a ton of weight savings, but would also require a lot of testing of sample pieces to get right. Especially if I want to try to get a similar level of strength as a fiberglass part, but with less layups.

## Ducted Propeller

This will likely be the first mod I try.

This would be adding an airfoil in the shape of a ring around the propeller to turn it into a ducted fan. Ducted fans are more efficient than standard propellers. The only question is how much more efficient this is, and is it worth the extra weight?

## Heated Canard, Wings, Strakes and Winglets

Slightly related to the "Make new lifting surfaces out of carbon fiber" is to embed heating material (I think I can use Carbon Fiber?) in the wings and run a current through them. This would serve as an anti-icing feature, making IFR flight much less scary.

There are a number of problems with this. Most obvious is I don't want to risk a runaway heater. If the heater gets too warm, then it can soften the epoxy and cause structural failure. I don't want to deal with temperature sensors that can potentially fail, so the best solution is to pass through a current/voltage amount that will never be enough power to heat the epoxy past the glass transition temperature. Depending on what material I use as the resistor, that depends mostly on the voltage.

Obviously, this would require a ton of time to get right, but this is one of the first things I want to investigate once I have a flying airplane.

## Larger Lifting Surfaces

Increasing the length of the lifting surfaces (main wings + canard) should result in both increased efficiency and an increased carrying capacity. Meaning increased battery capacity. I would have to do research to determine how much longer each should be. If you make the main wings larger without adjusting the canard, all you've done is make it easier to enter a deep stall. I'm less sure about the effects of a larger canard relative to the main wings, but I'm sure it's also not as desirable.

This would require a bunch of research to get right. Which means I'll put it off for quite some time.

## Motorized Landing Gear

This is an idea that's maybe on the "don't do" side, but there are a number of upsides to it and it might be worth the weight penalty. But electrically driven wheels would be great for ground operations. Using the propeller to taxi is very inefficient compared to directly driving the wheels. Additionally, this could be used to assist takeoff and landing by using the wheels for some small extra acceleration, as well as regenerative braking on landing.

However, this would add at least 30 lbs of weight to the system, which is not available. For an airplane that's being optimized for cruise flight, it seems silly to try to add some optimizations for ground operations.

## V2 Electric Airplane

This would be an entirely new airplane. One of the things I want to do with this is make a larger, 4+ person airplane. This would likely be made most of carbon fiber, with the battery compartment being lined with fiberglass (because fiberglass is non-conductive, unlike carbon fiber). Other thoughts include changing the fuselage side structure to make ingress & egress easier. As well as every other mod described here.

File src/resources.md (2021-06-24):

# Resources and Inspiration

## Links on building a gas-powered Cozy Mark 4

- <a href="http://www.cozybuilders.org" data-proofer-ignore>The unofficial cozy builders web site</a>, run by Marc Zeitlin.
- <a href="http://www.cozygirrrl.com/" data-proofer-ignore>Cozy Girrrls</a> makes and sells parts for the Cozy and other canards.
- <a href="http://canardaviation.com/cozy/" data-proofer-ignore>John Slade's</a> page on building his Cozy.
- <a href="http://www.canardaviation.com/PhillipJohnson/index.htm" data-proofer-ignore>Phillip Johnson's Kinda Kozy</a> has a subaru engine, fully retractable gear (which makes the cozy look so much better, even with the retracts deployed, a front hinge canopy w/ gull wing passenger entrance.
- [Cozy Serenity](https://cozyserenity.weebly.com) has a really detailed, modern build log. Definitely standing on the shoulders of giants type deal.
- <a href="http://www.eurekacnc.com" data-proofer-ignore>Eureka CNC</a> - this person built a CNC hot wire machine, and sells jigs that are CNC'd, or fully CNC'd out foam cores.

### Finishing

- [Wayne Hicks' Finishing Page](https://ez.canardaircraft.com/www.ez.org/pages/waynehicks/chapter_25_process.html)
- From <a href="http://curedcomposites.com/" data-proofer-ignore>Cured Composites</a>:
  - <a href="http://curedcomposites.com/finish.html" data-proofer-ignore>Finishing a Composite Airplane</a>

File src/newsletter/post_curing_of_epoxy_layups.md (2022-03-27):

# Post Curing of Epoxy Layups

From the Cozy Newsletter \#61

All epoxy systems have a minimum and a maximum curing temperature. At the minimum curing temperature, for example, room temperature, an epoxy system achieves a good degree of curing, that is, over 80%, and produces a hard, shiny, tack free surface, with good properties, but the properties, including glass transition temperature, are not maximized. For both L335 and L285, the properties achieved from room temperature cures are quite acceptable for aircraft use. The glass transition temperature of L335 after a room temperature cure, would be about 130 deg. F (the glass transition temperature is the temperature at which the epoxy begins to soften and become rubbery). To obtain 100% of the available properties and maximum glass transition temperature requires either post curing or curing at the maximum curing temperature. For L335, the maximum curing temperature or post curing temperature would be about 160 deg. F and results in a glass transition temperature of about 185 deg. F. But to achieve maximum cure and glass transition temperature, the layup would have to be held at the maximum curing temperature for about 16 hours. For L285 the maximum curing or post curing temperature would be about 170 deg. F and result in a maximum glass transition temperature of about 240 deg. F. Again, it would have to be held at the high temperature for about 16 hours.

So is it necessary to post cure your airplane? Actually, no. As either parts of your airplane or the entire airplane sit at temperatures above 70 deg. F, some post curing occurs. Even if your airplane sits outside in the sun, and the ambient temperature reaches 100 deg. F, it will do so gradually, and the post curing will proceed gradually so that glass transition temperature will always be considerably higher than ambient. The wings will not sag. Remember, you are going to paint your airplane white, and the surface temperature (only the top surface in the sun) will only get about 10 degrees higher than ambient. So on a 100 degree day, some post curing will already have occurred, so the glass transition temperature will already be higher than 130 deg. F and approaching the maximum of 185 deg. Now there is a possible exception to this rule. If you are going to paint your airplane black, or some other dark color, a fully post-cured L335 might not have a high enough glass transition temperature (185 deg. F might not be high enough). So, if you intend to paint your airplane black or some other dark color, you probably better use an epoxy like L285, and do some post curing before you park it out in the sun on a hot summer day. Remember, with an epoxy like L335, the glass transition temperature will always be higher than ambient and the epoxy will not soften unless or until the surface temperature reaches the maximum glass transition temperature, which in the case of L335 is about 185 deg. F. If you paint your airplane white, at least on the top, the surface should never reach this temperature even outside in Saudi Arabia in the summer. Even if you are not going to paint your airplane a dark color, but are willing to spend a little extra money on the best epoxy available, consider using L285. That would be our choice. If you do not understand, or have further questions, please contact us.

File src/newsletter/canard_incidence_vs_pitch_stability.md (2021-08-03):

# Canard Incidence vs. Pitch Stability

Copied verbatim from Cozy Newsletter \#72. Make sure this is done early in flight testing:

The Cozy Mark IV is designed to have positive pitch stability and to be resistant to a main wing stall throughout its approved c.g. range. But for this to be true, the canard must be set at the correct angle of incidence. During your initial flight tests, you should determine whether your canard is set at the correct angle of incidence, and there is an easy way to do this safely in flight. If you notice on large drawing M- 18, there is a protractor which shows the full travel of the elevator from minus 15 degrees at full forward stick to plus 30 degrees at full aft stick, and there is a notation that at cruise, the elevator should be in trail, i.e. at zero degrees. In newsletter #56, page 5, there is a plot of elevator position as a function of c. g. and speed for our plans-built model, and on this plot, the zero elevator position occurs at a c.g. of 101 and 150 knots IAS. For several years now, we have been including a copy of this page with each Owner's Manual. It also lists several changes for you to make to the Owner's Manual. So, before you expand your flight envelope, and before you fly at slow speed and aft c.g., check your elevator position. It is perfectly safe to do this at a c.g. of 101 and 150 kts IAS, or even better, at a c.g. of 100 and 150 kts IAS, your elevator position should be at less than minus 1 degree, i.e. about 1/16th inch trailing edge down. If your canard is set at too low an angle of incidence, it is a dangerous condition. The indication will be that the trailing edge of the elevator will be too low in cruise. The symptoms will be difficulty in rotating, pitch instability, and a tendency to react too fast to back stick. And the result could well be a main wing stall.

Very recently two builders complained of pitch instability, and difficulty rotating. I went for a demo ride with one of the builders in his Mark IV. With both of us in the front seat (and estimated c.g. of 100), the elevator trailing edge was down almost 3/8 inch or 5 degrees. For comparison, we both went up in our plans-built Cozy and the trailing edge of the elevator was zero to 1/16th trailing edge down. We concluded that his canard was set at too low an angle of incidence.
After a telephone discussion with the other builder, he sent me this e-mail:
"Hi Nat, Thanks for your input the other day. I adjusted the canard incidence by 2 degrees. Did so by relocating the guide bushings that engage the alignment tabs, as we discussed. Had to slightly modify the canard cover, but it was really much less of a task than I'd envisioned. Bottom line is that the aircraft now flies lovely all the way out to the forward c.g. limit. The c.g. and weight envelope is fully expanded as well as all flutter testing and low speed/min speed tests. Cooling is pretty good though I'm still working on it. Will provide more soon. Regards, Rob"

**This is an important matter. Make sure you check elevator position early in your flight test program.**

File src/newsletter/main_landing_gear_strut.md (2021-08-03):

# Main Landing Gear Strut

From the Cozy Newsletter \#78:

The FeatherLite main landing gear strut for the Mark IV is halfway between that of the Long EZ and Defiant in span, chord, thickness, weight, cost, and load carrying ability. It is made of S-glass and very dense, with no voids. It has an excellent spring-constant, and will not deform or take a permanent spread after repeated loading to many gs, nor should it be necessary to “set” the gear after parking. In newsletter #64-6 we explained how to measure wheel camber and suggested checking it annually to determine that no permanent spreading of the strut has occurred. We have yet to hear of a FeatherLite Mark IV strut taking a permanent set.

The strut was purposely designed with a return curvature at both ends to reduce local bending loads. This also results in the wheels having a slight camber (bottoms closer together) of about 2.5 degrees when the Mark IV is empty or slightly loaded. As the loading is increased, the strut spreads and the wheels move outboard and become closer to vertical. As the loading is further increased, like in a high-g landing, the strut has been known to spread enough for the inside of the wheel pants to scrape the runway, and in very extreme cases, spread enough for the brake calipers to scrape the runway. But always the strut should return to its original shape after the load is relieved.

Tire wear is always the greatest at the instant the tire touches the runway, because wheel rotation is instantly accelerated from zero to about 70 knots. Because of the camber of the wheels, which is even greater when the airplane is in the air just before touchdown, the outboard tread receives the greatest wear. So when the outboard tread is nearly worn away, it is the accepted and recommended practice to reverse the tires (outboard to inboard) to even out the wear, similar to what you do with your automobiles when you rotate the tires.
Before installation of the strut, you are instructed to wrap it with 8 crossing plies of UNI, to increase the torsional strength. This should eliminate or at least minimize any possibility of wheel shimmy. You should not substitute BID, Bi-Ax, or Tri- Ax cloth.

You are instructed to install the axles with a slight toe-in, about 1⁄4 degrees. This will provide the least rolling resistance in takeoff and landing, and least tire wear. When you think about it, the reason is simple. During takeoff, as the load is relieved from the wheels, the strut tries to come together, and toe-in helps it do that. When you land, the sudden load (unless you “grease it on”) spreads the strut and then as the load is relieved, the toe-in helps it come together.

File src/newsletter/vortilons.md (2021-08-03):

# How do you make Vortilons

From Cozy Newsletter \#77:

A way that works well is to make a flat 3-ply 8 x 8 layup on a piece of plastic, and then cut out a pair of each of the 3 vortilons (see M-18). Then tape saran wrap on the leading edge of the wings at each of the 3 locations. Use a generous amount of saran. Then put down a 2-ply layup over each of the saran wraps on the leading edge of the wing. Make it generous, and use peel ply over the top. Sand the vortilons. After the leading edge layups have cured, remove the peel ply and 5- minute the vortilons to the leading edge layups, using the 67 degree template on M-18 to make sure they are at the right angle. After all are in place with the right alignment, micro the inside corners and tape both sides of the vortilons to the flanges with 2 plies of BID, and peel ply. After cure, remove the flange-vortilons from the leading edge, and trim the flanges to about 3⁄4” width each side of the vortilon. Paint them. After the wings are painted, stick them on with clear silicone. They will adhere without coming loose even after many head bumps. Put them on before you fly and never take them off!

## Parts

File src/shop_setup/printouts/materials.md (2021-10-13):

<style>
.section_list {
    display: flex;
    align-items: flex-start;
    flex-wrap: wrap;
    margin: 16px;
    align-content: space-around;
}

.section_content {
    margin: 4px;
    max-width: 48%;
}

.section_list.nowrap {
    flex-wrap: nowrap;
}

.nowrap .section_content {
    flex: 1;
}

@media print {
    .pagebreak { page-break-before: always; } /* page-break-after works, as well */
}
</style>

# Materials

<!--

This is meant to be printed out and displayed in the shop.
-->

<div class="section_list">
<div class="section_content">

## MGS 335 Epoxy

The MGS 335 Epoxy should be mixed at a 100:38 resin:hardener ratio. This means the following:

| Total Epoxy | Resin | Hardener |
|---|---|---|
| 60 g (~2 oz)  | 43.48 g  | 16.52 g  |
| 120 g (~4 oz) | 86.96 g  | 33.04 g  |
| 180 g (~6 oz) | 130.43 g | 49.57 g  |
| 240 g (~8 oz) | 173.91 g | 66.09 g  |

Don't try to mix more than 8 ounces (~240 g) in a batch. If your layup requires more than 8 ounces, make multiple batches. Mix enough epoxy for a 3:4 ratio of epoxy to fiberglass by weight (that is, mix 75% as much epoxy as fiberglass by weight).

</div>
<div class="section_content">

## Slurry, Wet and Dry Micro

Mix the glass bubbles with already-mixed epoxy.

| Material  | Desired Consistency | Ratio (Balloons:Epoxy) (by volume) |
|---|---|---|
| Slurry | Almost same as epoxy | 1:1 |
| Wet Micro | Sags or runs like thick honey  | 2-4:1 |
| Dry Micro | Paste that does not run or sag | ~5:1 |

Apply Dry Micro with a putty knife. Apply Wet Micro and Slurry with brushes.

</div>
<div class="section_content" style="max-width:100%">

## Flox

As with Slurry and Micro, mix the flocked cotton with already-mixed epoxy.

| Material | Desired Consistency | Ratio (Cotton:Epoxy) (by volume) |
|---|---|---|
| Flox | Just enough to make the mixture stand up | ~2:1 |
| Wet Flox | Sag or Run | |

When using flox to bond a metal part, be sure to sand the metal dull with 220-grit sandpaper. Also paint pure epoxy (no flox) on the metal part prior to bonding with flox.

</div>
</div>

# Safety

<div class="section_list nowrap">
<div class="section_content">

### MGS 335 Material Safety Data Sheet

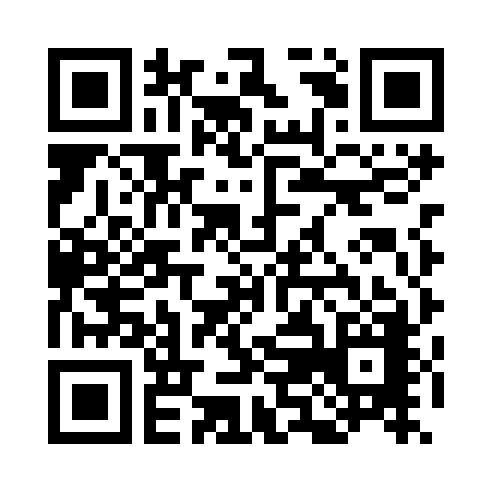
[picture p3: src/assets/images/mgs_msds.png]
MGS 335 Material Safety Data Sheet (https://www.aircraftspruce.com/catalog/pdf/LH335MSDS.pdf)


&nbsp;

</div>
<div class="section_content">

### 3M Glass Bubbles

Wear googles and dust mask when mixing!

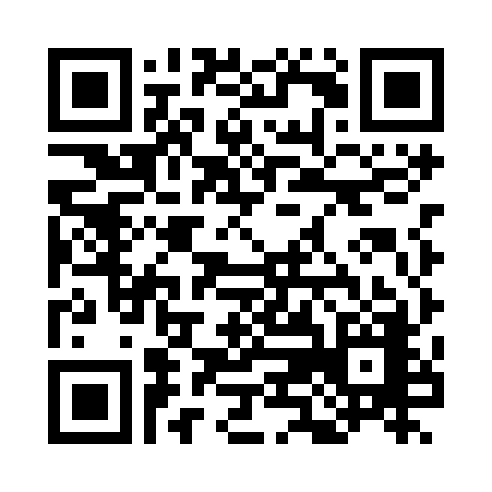
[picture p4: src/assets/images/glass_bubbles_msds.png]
3M Glass Bubbles Material Safety Data Sheet (https://www.aircraftspruce.com/catalog/pdf/3mbubblessds.pdf)


</div>
</div>

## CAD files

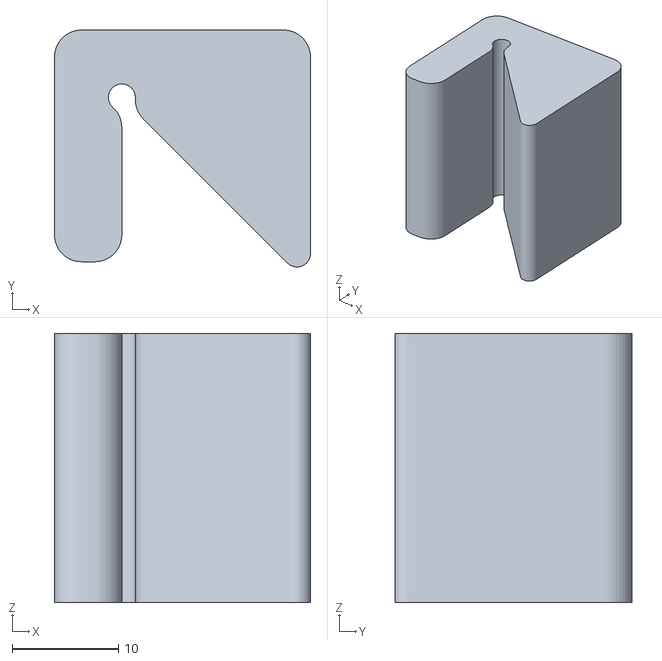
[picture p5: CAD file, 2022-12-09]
src/assets/cad/chapter_5/lower_longeron_clamp_jig.stl
24.1 x 22.3 x 25.4

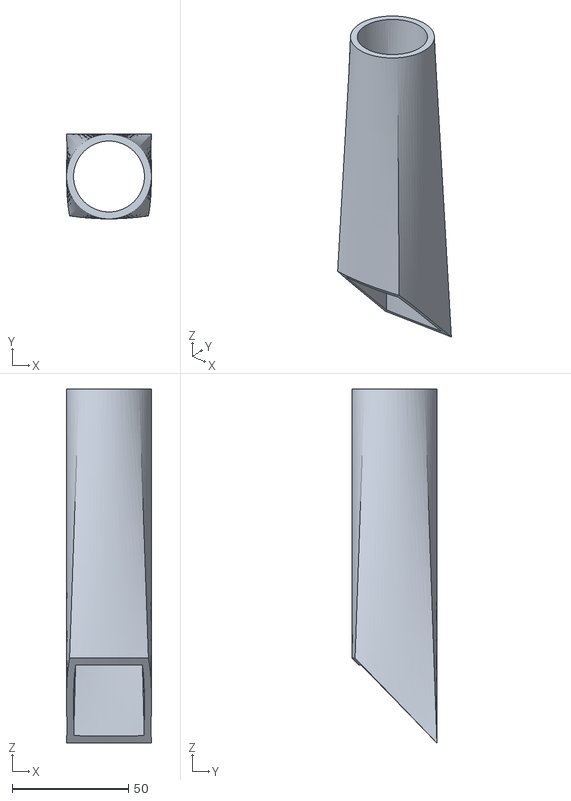
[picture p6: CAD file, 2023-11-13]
src/assets/cad/chapter_8/Duct Transition Plug.stl
36.5 x 36.5 x 152.4

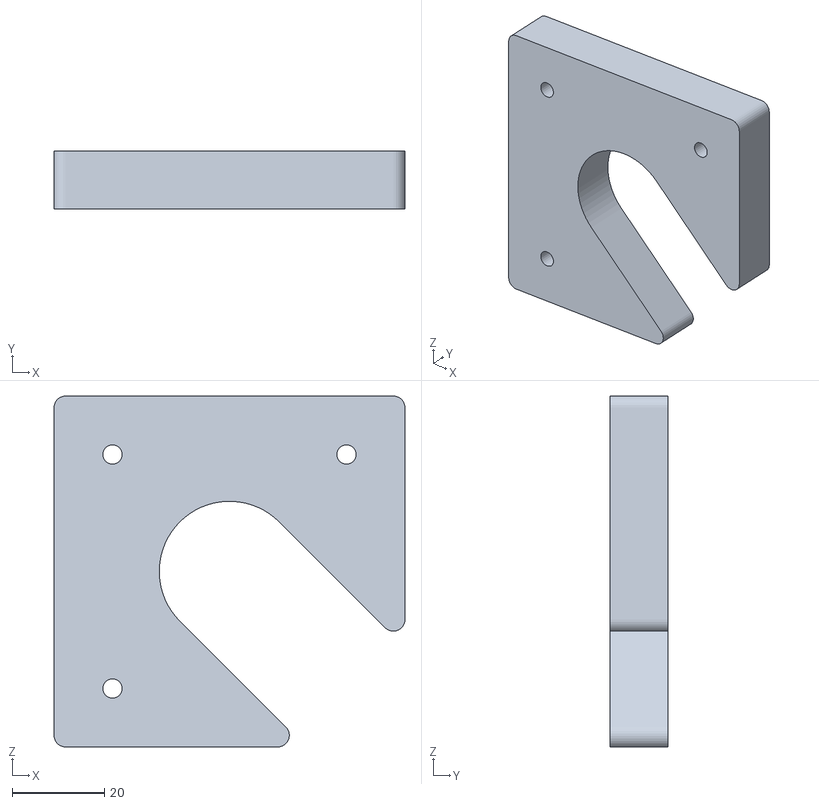
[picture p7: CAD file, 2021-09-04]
src/assets/cad/dowel_mount.stl
76.2 x 12.7 x 76.2

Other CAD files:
src/assets/cad/workbench/workbench_v1.0.f3d
src/assets/cad/workbench/workbench_v1.4.f3d
src/assets/cad/workdesk/workdesk_v1.f3d

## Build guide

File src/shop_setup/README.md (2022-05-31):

# Shop Setup

Here's how I set up my shop for this:

You'll need a lot of workbench space. I [designed my own 2'x4' workbench]({{#path_for Workbench}}), and plan to build 6 of them.

Additionally, you need a bunch of storage space. I built a [cabinet to store fiberglass in]({{#path_for Fiberglass Cabinet}}), which has space underneath it. I store store epoxy supplies underneath it - extra resin/hardener, flocked cotton for flox, microspheres for micro, etc. I also have a 3d printer under there, which is currently unused in this project. Though, I'll probably 3d print some jigs.

I've also built a nice box where I have a container each of epoxy resin and hardener, wrapped in a heating pad. When I'll be doing work with epoxy, I turn on the heating pad in the morning, and by lunch the epoxy has heated up enough to be usable. The box is made by cutting half-inch plywood and joining together with glue and screws. Nothing special. The back of it has a cut out for the heating pad + wire to go through, and there's a door on the other side, which friction-fits closed (there's no latch to keep it closed). It's not great construction, but it's fine for the purpose.

Future known work includes:

- More storage. You will always need more storage.

Additionally, I also have some [printouts of information good to have visible in the shop](./printouts/index.html).

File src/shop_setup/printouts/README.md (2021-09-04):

# Printouts

Notes to print out and place in a visible place in the shop.

Here we have:

- [Materials](materials.md) is good info on making epoxy, with QR codes for the epoxy and glass bubbles MSDS.
- [Basic Layup Procedure](layups.md) is more-or-less a transcription of Chapter 3, page 19. I didn't want to rip it out of the plans and hang it out on the wall.

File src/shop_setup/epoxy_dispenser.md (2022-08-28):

# Automated Epoxy Dispenser

When you use a traditional epoxy pump, there's no way to tell if it actually dispensed in the correct ratio until the epoxy has cured. If there's some kind of blockage in one of the pumps, you won't find out until the epoxy has cured, and you find out it didn't cure correctly. Because of this, you need to calibrate the pumps regularly.

Still, fear of this is why I elected to use a scale and manually pour epoxy using a scale to measure it. However, manually pouring epoxy is a bit of a skill. Not a hard skill to learn - I had basically mastered it by the fourth or fifth time I mixed epoxy. But it's a bit annoying and time consuming. Certainly, pulling levers for epoxy pumps is significantly easier to do, and it takes significantly less time to do so. I wanted something even easier, even if it's still not as fast. As a wannabe electrical engineer, I decided to build an automated epoxy dispenser.

So, I bought some peristaltic pumps and some other components, and I made the simplest "press button, receive epoxy" program I could think of.

## Current State

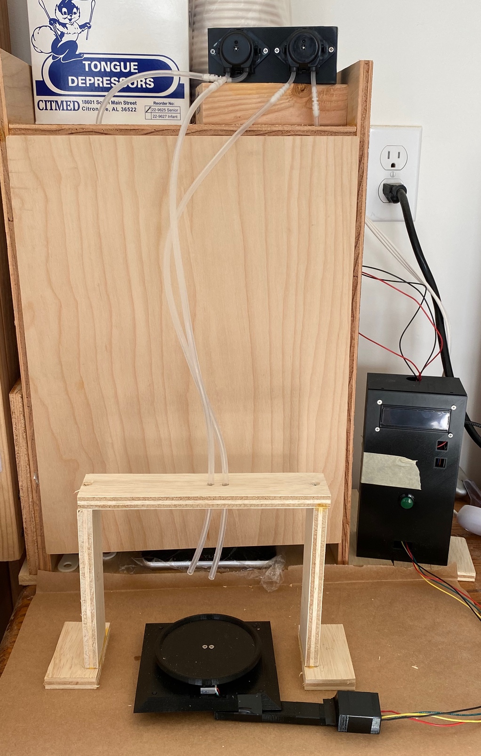
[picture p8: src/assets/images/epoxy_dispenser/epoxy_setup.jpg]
Image of the Epoxy Dispenser in place, with the pumps on top of the epoxy box, the control electronics on the right, and the scale towards the bottom


The epoxy dispenser I built works very well. With the press of a button (the green button on the box on the right), it starts dispensing. Currently, it's set to dispense 120 grams (about 4 oz) total of epoxy and hardener. While it does take quite some time to dispense (approximately 10 minutes), it's worth it to not have to manually pour epoxy. This would be an issue if I used epoxy with a faster working time, but the MGS 335 system I use has a working time measured in hours.

### Hardware

This uses 2 peristaltic pumps to dispense epoxy. [Wikipedia has a pretty good article about them](https://en.wikipedia.org/wiki/Peristaltic_pump), but peristaltic pumps work by squeezing a plastic tube to force fluid through it. This makes them great for a ton of applications where you want to pump something, but you don't want to expose the pump itself.

These pumps are controlled by an arduino clone, using an L293D motor driver chip. This is a common driver chip and it lets me to control a motor from a low-amperage-output control pin.

On the sensing side, I have a basic load cell hooked up to an HX711 amplifier chip.

The arduino clone reads the load cell (via the HX711 chip), and then uses that to determine which pump to run, as well as what speed to run it at.

### Program

The control program runs at a rate of 10 hz. Each loop, it samples the scale to get the current total weight, and runs that through a PID loop to determine how quickly to run the chosen pump. Additionally, it also updates the character display with information about the current state of the system, as well as how much of resin or hardener it has dispensed.

On a higher level, the program is a simple state machine: It boots up into the IDLE state, where does nothing but take measurements from the load cell and display them on the character display. This makes the program useful for manually pouring epoxy, on the occasions I need to do that. When you press the green button, it changes to the RESIN state, where it runs the resin pump. Once the controller has detected that enough resin has been dispensed, then it switches over to the HARDENER state, where it turns off the resin pump and runs the hardener pump. Once the controller detects that we've dispensed enough hardener, it switches to the SHUTDOWN state, where it turns off all pumps and resets back to the IDLE state.

### Issues

As much as I like this system, it's not without issues. On the software side, I don't have a way to pause dispensing without stopping and resetting. So if I run out of either resin or hardener mid-pour, then I need to either throw away what was already dispensed, or manually finish the pour. On a future revision, I may add a switch to allow me to pause without resetting.
Another feature I'd like is the ability to specify an exact amount of either resin or hardener to be dispensed. Both of these are useful for solving the issue of running out of either material.

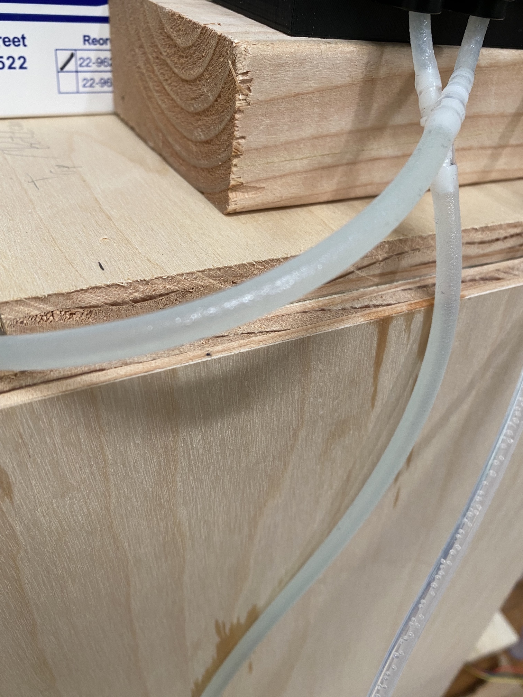
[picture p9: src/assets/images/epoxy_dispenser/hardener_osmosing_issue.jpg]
Epoxy Hardener crystalizing on the plastic tubing


More worryingly than issues replacing the contains, the epoxy hardener I use appears to be able to permeate through the plastic of the pumps. Which makes me worry that it might lead to gumming up the pump, potentially breaking it or causing some other issue. This appears to be the same issue that [@cyanoacry on twitter](https://twitter.com/cyanoacry) ran into [when he tried this same idea](https://twitter.com/cyanoacry/status/1520564688840396800), though he's using a slightly different epoxy system. I've attempted to resolve this issue by using different tubing materials. At the moment, the I've gone through every tubing material I could find on McMaster Carr, and none of them completely solve the issue. The best I've come across is black rubber tubing, which lasts about 3 weeks before enough permeates through that I need to replace it. Thankfully, the epoxy resin does not appear to have this issue at all, and has been perfectly fine with the silicone tubing that came with the pump.

I'm willing to accept this and resign myself to replacing the tubing twice a month, that's still plenty of time.

## Future Work

I'd love to improve this and make it more versatile, some ideas for future work include:

- Redesign the system to have all components on a single board, instead of connecting different breakout boards.
- Add a UI for dynamically configuring different mixtures of epoxy.
- Add support for another motor, so that I can mix fast and slow hardeners for a configurable pot life.
- Add buttons for shortcuts for different predefined mixtures.

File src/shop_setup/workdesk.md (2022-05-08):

# Workdesk

A simple workdesk on wheels with pegboard backing.

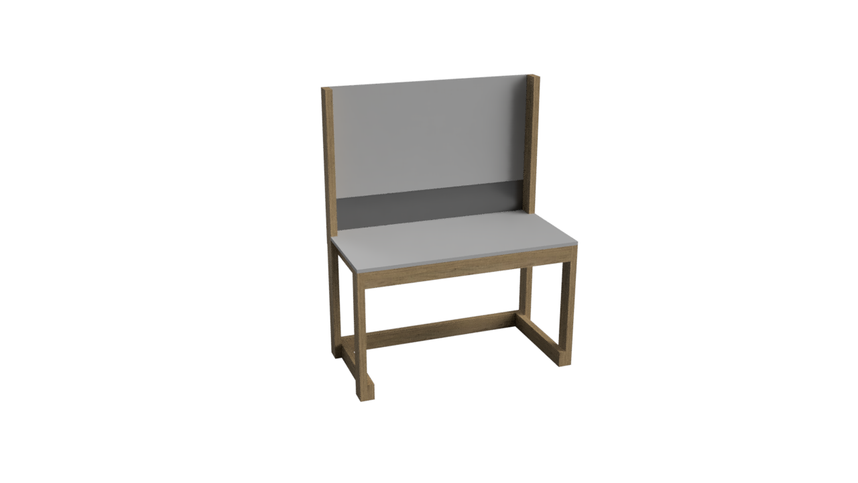
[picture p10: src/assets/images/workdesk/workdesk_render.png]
CAD rending of the desk


- [USDZ (AR Preview)](/assets/cad/workdesk/workdesk_v1.usdz)
- [Fusion 360 file](/assets/cad/workdesk/workdesk_v1.f3d)

This project happened because, while I had quite a few workbenches made already, I wanted something that would also be more of a designated soldering station. As well as a place to store tools and other things so that they're not just sitting on one of the workbenches.

### Materials

As with the workbench, this is constructed primarily with 2x4 studs, and uses a 2' by 4' sheet of 3/4" plywood as the tabletop.

- 2x4 studs.
  - 2x 60" studs (the rear legs). (1)
  - 2x 28" studs (the front legs)
  - 3x 45" studs (the cross supports)
  - 3x 21" studs (the top depth supports)
  - 2x 22.5" studs (the bottom depth supports)
- Plywood/planes of wood
  - 1x 48" by 24" by 3/4" sheet of plywood (top surface)
  - 1x 48" by at least 8" by any thickness sheet of plywood (to catch things from rolling off the back) (1)
  - 1x 48" by 24" sheet of pegboard (1)
- Extra hardware
  - 4x castering wheels, to make it easier to move around.
  - Many 3" screws.

(1): You can change the height of the rear legs to whatever you want. If you don't need a backing (i.e. basically making another workbench), you can leave it at 28" to match the front legs. It should be at least as high as the front legs height (28") + the depth of the tabletop (3/4") + however high your pegboard is (in my case, 24") + any amount of "gap" between the bottom of the pegboard and the tabletop. Having a gap is desirable as it lets you better utilize the pegboard. The plans here specify 60" because it's easy to remember.

### Instructions

This is intended to be as simple as possible.

1. Use woodglue (you can dilute it 1:1 with water to make it easier, but I generally choose not to do this) on the endgrains of the cross and depth supports. This makes drilling into the endgrain result in a much stronger joint.
2. Top Frame
  - Line up the cross supports (the 45" pieces) and depth supports (the 21" pieces), with the depth supports inside of the cross supports, and 2 of the depth supports on either end, and the third in the center. Join them together with woodglue, then use screws to secure that connection. I simply screwed into the end-grain. Which isn't that great of a bond. You could use pocket screws from the other end and it would be a much better joint. Either way works just fine for this.
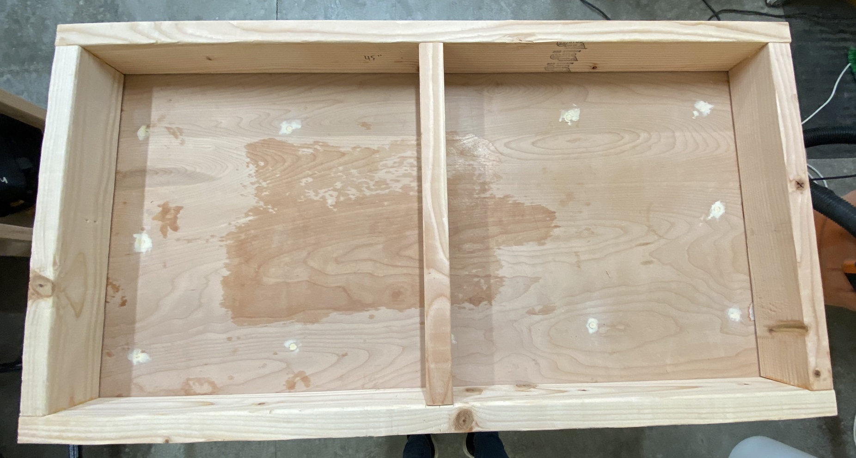
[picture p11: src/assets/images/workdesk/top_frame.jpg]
Top-down view of top frame
  
3. Bottom frame
  - Line up the cross support (45" piece) and bottom depth supports (the 22.5" pieces), similar to the top frame. Only this time, because there's no center depth support, and only one cross support. That lack of extra cross support is why these depth supports are an extra 1.5 inches longer. Join them with woodglue and screws.
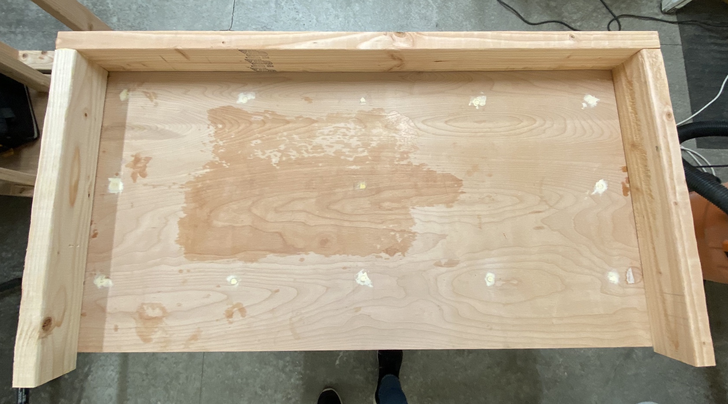
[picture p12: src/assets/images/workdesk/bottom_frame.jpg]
Top-down view of bottom frame
  
4. Rotate the frames so that their fronts are facing down, and line up the front legs so that you can easily attach them using woodglue & screws.
  - Installing the front legs first is recommended because the back legs, by virtue of being longer, are heavier and make the whole thing more unwieldy to move about.
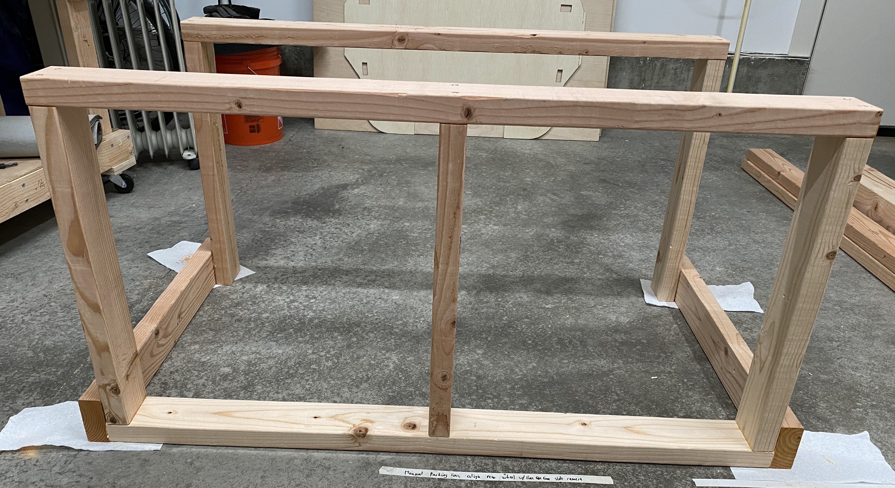
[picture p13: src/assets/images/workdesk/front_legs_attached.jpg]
View of the frames aligned with the front legs attached
  
5. Rotate the assembly again so that the backs are on the ground, facing down. Install the rear legs similar to how you installed the front legs.
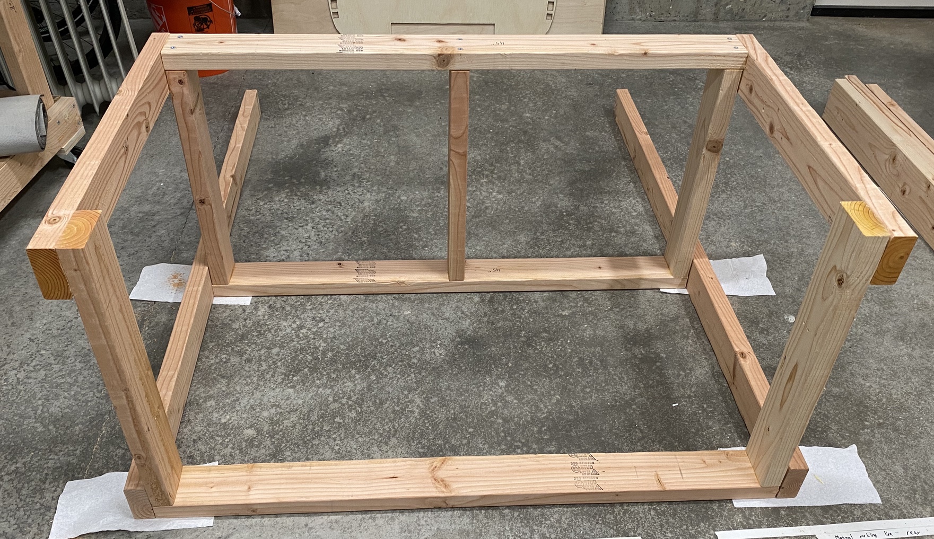
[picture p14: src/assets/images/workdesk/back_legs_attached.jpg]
view of the frames with the back legs attached
  
6. While the desk is on its back, install the front wheels. Then rotate it again and install the back wheels.
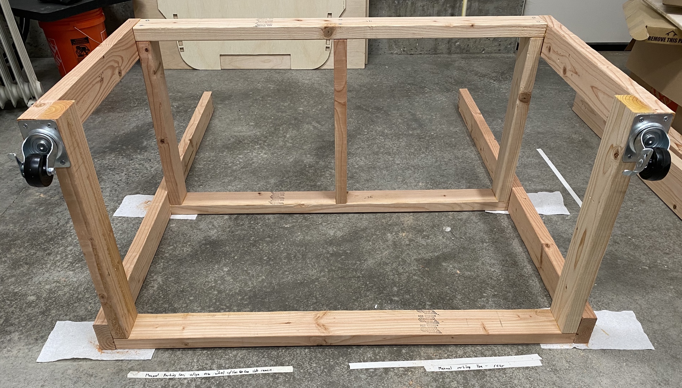
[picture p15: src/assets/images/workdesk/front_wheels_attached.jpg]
view of the frames with the front wheels attached
  
7. Rotate the desk so that it's upright.
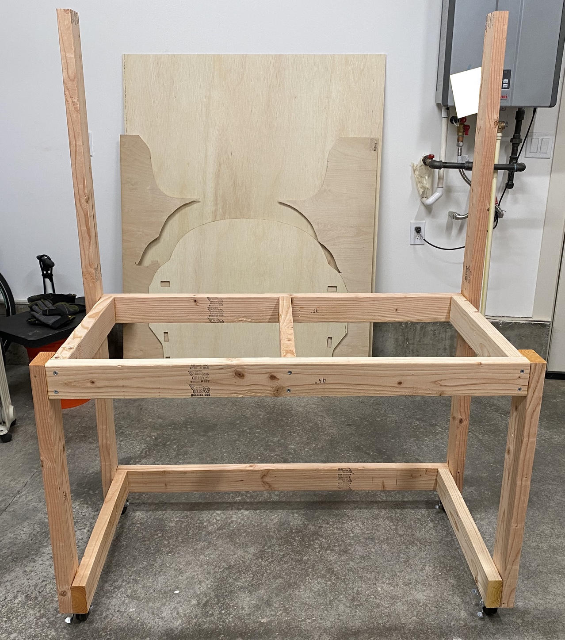
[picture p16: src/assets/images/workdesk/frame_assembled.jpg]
view of the frames assembled with wheels attached
  
8. Cut 2 1.5" x 3.5" tabs into the back of the tabletop such that it'll fit nicely into the top of the desk with no overhangs on the front or rear.
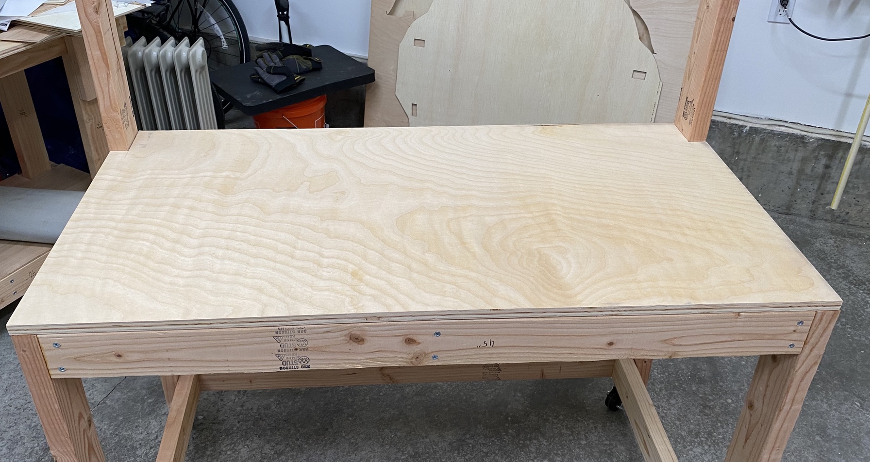
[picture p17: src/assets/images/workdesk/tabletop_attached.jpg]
View with the tabletop in place
  
9. Get a friend to help you as you screw in the pegboard into the top of the rear legs.
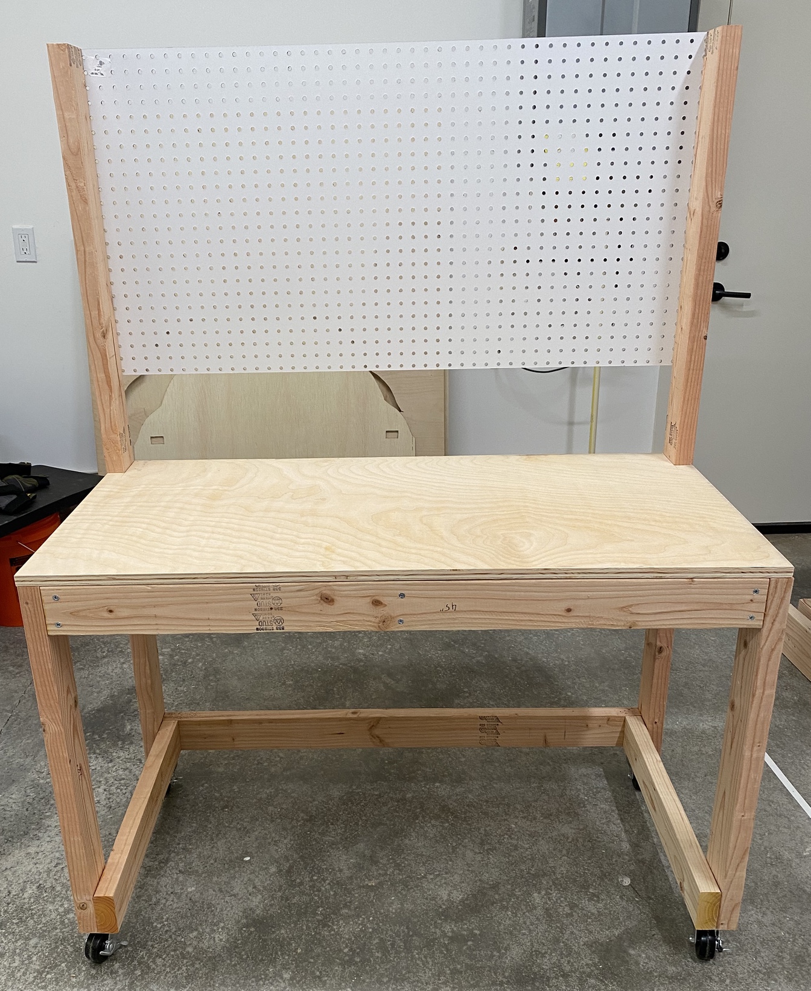
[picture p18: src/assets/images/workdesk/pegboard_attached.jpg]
Desk nearly finished with the pegboard in place
  
10. Install the "backguard" piece by screwing it in. You can add woodglue (or just actual caulk) as caulk to make sure that any small pieces that land back there don't fall off the back.
11. Screw the tabletop into the top frame. Don't glue it in so that you can easily replace it in the future.
12. Paint or finish it as desired. Be sure to sand down the rough edges prior to use.

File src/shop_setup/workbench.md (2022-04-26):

# Workbench

These are heavily inspired by the [EAA Chapter 1000 Standardized Work Tables](https://www.eaa.org/eaa/aircraft-building/BuilderResources/while-youre-building/building-articles/tools-and-workshop/worktables), only designed to to be 2 feet by 4 feet instead of 2 feet by 5 feet. A bunch of people in the cozy community prefer joining 6 tables of these size to ultimately create the plans-recommended 12 foot by 4 foot table for the wings and other large pieces. This is my take on that.

## Version 1.4, April 2022

Starting on the fifth table, the primary goal is to simplify construction by removing the use of half-laps entirely. Here's what I came up with:

- Extend the lip of the top frame to line up with the tabletop.
- Do away with resting the top frame on the legs. Screw the top frame into the legs.
- Increase the size of the bottom frame to match the
- Build the bottom frame into the legs.
- Use height-adjustable casters. Screw them into the bench using t-nuts.

Here's image of what I came up with:

CAD rendering of workbench

- [USDZ (AR Preview)](/assets/cad/workbench/workbench_v1.4.usdz)
- [Fusion 360 file](/assets/cad/workbench/workbench_v1.4.f3d).

None of these previews include the wheels, because my CAD-fu isn't good enough.

### Materials

- 2 by 4 studs
  - 2x 48" studs (the top frame rails)
  - 3x 21" studs (the top frame spans)
  - 2x 38" studs (the bottom frame rails)
  - 3x 18" studs (the bottom frame spans)
  - 4x 28" studs (the legs)
- Plywood
  - 1x 48" by 24" by 3/4" plywood (the top surface)
  - 1x 45" by 21" by 1/4" plywood (the bottom shelf)
- Extra hardware
  - 4x castering wheels with center screw
  - 4x t-nuts which fit those center screws
  - Many screws
  - Optional: Pocket hole jig + pocket hole screws (for securing things to the legs).

### Instructions

1. Top Frame:
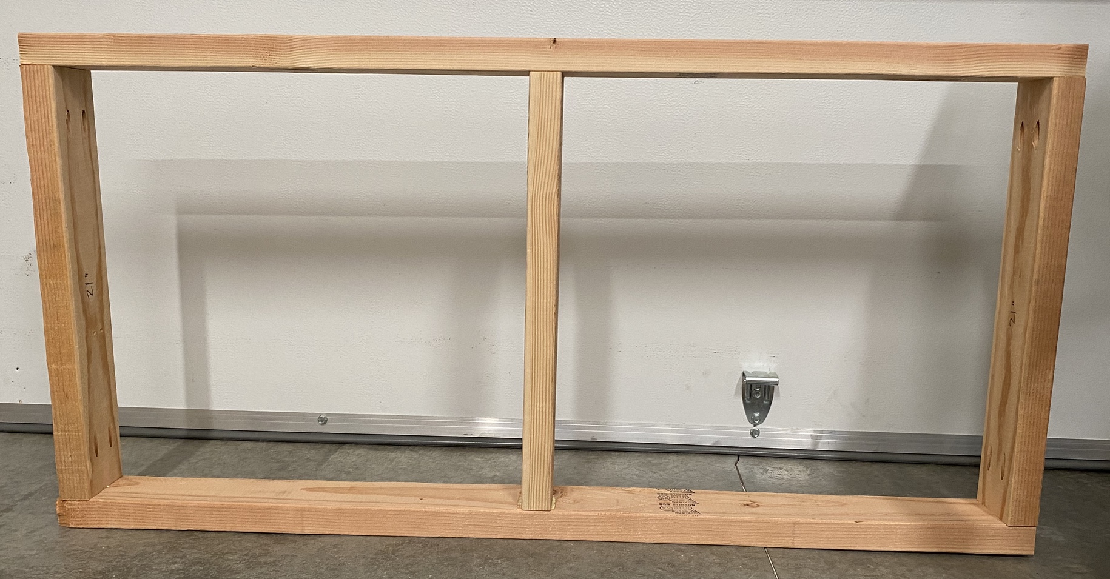
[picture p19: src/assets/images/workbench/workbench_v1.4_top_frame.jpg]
Photo of the top frame laying on a side
  
  - Screw the top frame pieces together. Remember that the spans go inside of the rails.
2. Bottom Frame:
  - Screw the bottom frame pieces together. The rails screw into legs, same with each edge span.
3. Placing the bottom assembly on the floor, place the top frame in place (the tops of the legs should meet at the 4 inner corners of the top frame). Make sure that the top of the top frame to be flush with the top of the legs. It'll help to use scrap wood to hold the frame on the legs. Screw the top frame into the legs from both the rails and the edge spans.
4. Re-orient the frame to be upside down. Drill a hole in each leg, then put in a t-nut. Add a nut to the caster, then screw that in as well. The nut makes it a lot easier to lock in a height once you have the desired height.
5. Re-orient the frame back to normal. Screw the benchtop into the top frame.
6. Cut 1.5" by 3.5" tabs into the bottom shelf top, then slide that in to rest on the bottom frame. No need to screw this in, the legs of the table will keep it from moving around too much.

## Version 1.3, March 2022

On the fourth table I built, I had what's really the second meaningful change to the design of my tables This results in a larger bottom shelf, and a much easier build process. There's still work to improve the build process and make that easier, which will be part of the version 1.4 design.

In this version, the top is still made using half-laps, but the bottom-shelf frame is joined using butt-joints and mostly screws.

### Materials

- 2" x 4" studs
  - 2x 48" studs
  - 3x 24" studs
  - 4x 28" studs
  - 2x 40" studs
  - 3x 16" studs
- Plywood
  - 1x 48" x 24" x 3/4" plywood (you could also use 1/2" plywood and it wouldn't matter)
  - 1x 40" x 19" x 1/4" plywood
- 4x 3.5" tall castering wheels.
  - Get t-nuts and wheels with screws in them. This way, you have height-adjustable wheels that make aligning each table in height significantly easier.

As before, get large studs and cut them to size. You can make this with 6x 8' studs. You can also use 10' or 12' long studs and cut them to size. Whatever will fit in your vehicle. Similarly, it's much more economical to get 4' by 8' sheets of plywood, instead of project boards.

### Instructions

1. Top Frame
  - Cut half-laps into the 48" studs. These will have a depth of 1.75" (half the height of the studs). They should be 1.5" long (the width of the studs). Cut 2 of them 4" from the edges, then a third in the exact center of the 48" stud (starts 23.25" from either edge). Make these cuts all on the same side.
  - Cut rabbets into 3 of the 24" studs. These will be at the ends of the studs. As before, they'll be 1.75" deep, and 1.5" long. Make these cuts all on the same side.
  - Join the 48" studs with the 24" studs you just cut into. The correct orientation for this is that the 24" will slot down into the 48" (so that, when weight is placed on the 24" studs, they'll transfer that weight into the 48" studs)
2. Bottom Shelf
  - Butt together the 40" studs and the 16" studs such that the 16" studs are in between the 40" studs. Screw them together. Optionally, you can glue them, but honestly, that's not necessary.
3. Legs
  - The legs should be oriented so that the height of them (the nominally 4"/actually 3.5" side) is parallel to the 40" studs/the length of the table.
  - With the bottom legs flush to the bottom of the bottom shelf, and extending straight up, glue and screw them in to the bottom shelf.
4. Wheels
  - With the table inverted (resting on the top of the table), install the castering wheels + any shim material onto the bottom of the bottom shelf.
    - Make sure the caster wheels are installed so that most, if not all, of the weight from the top surface is transferred directly to the wheels. (If you get casters that have a single screw going up through them - which you should, because that makes adjusting the height easier - then predrill & install a t-nut going through any shim material and into the legs.)
5. Installing the Top Frame
  - Revert the table so that it's on its wheels. Lock them at this point (and also brace the table so that it still doesn't move unnecessarily)
  - You should be able to place the top frame directly on the legs at this point. It should just line up. Obviously, this isn't a long-term solution.
  - Using scrap pieces, add brackets to the outside of the legs. These will actually hold the top frame in place and keep it from sliding around. I used 2x4s, but if you have any scrap 3/4" plywood, you could cut it to size and use that.
  - Place the top frame back onto the legs, and screw the brackets into the top frame.
6. Surfaces
  - Cut out rectangles in the corners of the bottom 40"x19" sheet so that it'll actually fit into the bottom shelf.
  - Screw the 48"x34" sheet into top of the frame. I added screws at where the 24" studs intersected with the 48" studs.
  - Slide the bottom 40"x19" into the bottom shelf.

### Future Thoughts

Some thoughts I have on improving this one:

- I should entirely remove the need for the half-lap joineries. It would allow me to create a more precise table, as getting the depths of these cuts correct is difficult.
- I should use height-adjustable locking casters. This requires some additional hardware, but makes finely aligning individual tables possible. I'm going to go back and add these at a later date to my tables, where possible.

Because of both, expect to see a version 2.0 sometime in the future, as I create additional workbenches.

## Initial Version, July 2021

Initially, I designed these to basically join using half-laps. Essentially, each wood stud would have either dados or rabbets cut into them, then I'd join them together using glue and screws. This makes for a very strong table, but it's more than I need. Archived here is the initial table version.

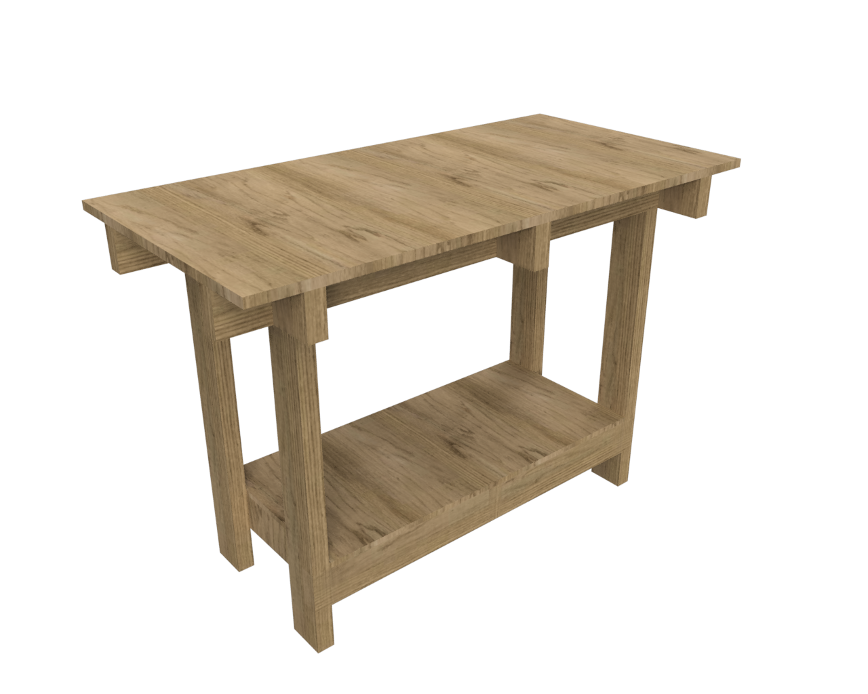
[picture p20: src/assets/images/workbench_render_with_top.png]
CAD rendering of workbench


- [USDZ (AR Preview)](/assets/cad/workbench/workbench_v1.0.usdz)
- [Fusion 360 file](/assets/cad/workbench/workbench_v1.0.f3d).

### Materials

This is made using 2x4 studs and plywood, held together using simple woodworking joints, with wood glue and screws to supplement.

- 2" x 4" studs (which should actually measure 1.5" x 3.5")
  - 2x 48" studs
  - 3x 24" studs
  - 4x 32" studs
  - 2x 37" studs
  - 3x 16" studs
- Plywood
  - 1x 48" x 24" x 3/4" plywood "project board".
  - 1x 34" x 16" x 1/2" plywood "project board".

To minimize material needed to buy, you can buy 6x 8' studs, and have the lumber yard cut them to size. Additionally, for the plywood, it's significantly cheaper to buy 4' by 8' sheets (oftentimes, these sheets only cost about twice as much as a project board, but you get 4 times as much material), and either cut them down yourself, or have the lumber yard do so on site. Most places won't charge you to get the wood cut.

After the initial table, in the next 2 versions, I added 4x 3" castering wheels to each table. This required cutting the 32" studs to only 28", and some additional spacers between the bottom of the studs holding the bottom shelf and the wheels.

### Instructions

First, we're going to build the frame, then screw in the table and shelf tops.

1. Top Frame
  - Cut half-laps into the 48" studs. These will have a depth of 1.75" (half the height of the studs). They should be 1.5" long (the width of the studs). Cut 2 of them 4" from the edges, then a third in the exact center of the 48" stud (starts 23.25" from either edge). Make these cuts all on the same side.
  - Cut rabbets into 3 of the 24" studs. These will be at the ends of the studs. As before, they'll be 1.75" deep, and 1.5" long. Make these cuts all on the same side.
  - Join the 48" studs with the 24" studs you just cut into. The correct orientation for this is that the 24" will slot down into the 48" (so that, when weight is placed on the 24" studs, they'll transfer that weight into the 48" studs)
2. Legs
  - Cut rabbets and half-laps into the 32" (or 28") studs. These will have a depth of 1.5", and a length of 3.5". The half-lap should be made on the other end (but same side) of the stud. The half-lap cut should be inset 4" from the end it's cut on.
    - If you instead intend to install castering wheels, both ends of the 28" studs will have these rabbets cut at their ends.
  - Join the rabbet from these studs into the inside corners of the 48" studs and the 24" studs of the top-frame.
3. Bottom Shelf
  - Cut 3 half-laps into the 37" studs. All these should be 1.75" deep, and 1.5" long. 2 of them should be inset 1.5" from the ends, and the third should be in the dead center (starting 17.75" from the ends).
  - Cut 2 rabbets into the 16" studs. Similar to above, these should be 1.75" deep and 1.5" long.
  - Join the 37" studs into the legs from earlier, into the unused half-lap cuts near the bottom.
  - Join the 16" studs into the 27" studs.
4. (Optional) Installing castering wheels:
  - With the table inverted (top on the ground):
  - Add the shim material (enough to cover the distance between the 4" from the bottom of the shelf-studs to the floor, minus the height of your casters. In my case, the caster wheels, including hardware, were 3.5" tall, so I added 0.5" of shim material).
  - Predrill wholes for the casters, and screw them in.
5. Surfaces
  - Cut out rectangles in the corners of the bottom 34"x16" sheet so that it'll actually fit into the bottom shelf.
  - Screw the surfaces to their respective places (the 48"x24" plywood sheet should screw into the top, the 34"x16" sheet should screw into the bottom).
    - It's actually entirely unnecessary to screw the bottom sheet into place. It'll be held in place by the legs on the bottom.

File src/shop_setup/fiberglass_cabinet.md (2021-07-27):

# Fiberglass Cabinet

Unlike the workbench, this is joined mostly with butt-joints. This doesn't need to support a ton of weight, so butt joints held together with glue and screws is perfectly fine for this.

## Bill of Materials

First, the actual materials and lengths needed to construct this. This is made primarily with 2x4 studs (which are actually 1.5 x 3.5 inches, because of course they are).

2x4 studs:

- 2x 60" (for the backplate)
- 2x 33.5" (for the front support)

- 2x 30" (Giving extra depth for the fiberglass container)
- 6x 48" (4 for the "rails" supporting the front and back of both the top surface and the bottom shelf, then 2 for the top part, covering the fiberglass container)
- 6x 24" (the "ribs" of the top surface and the bottom shelf)

Plywood. half-inch or even quarter-inch is fine.

- 2x 48" x 27" sheets (The shelves)
- 1x 48" x 31" sheet

Extra:

- Screws. I used 3 inch \#8 screws for most of the frame. For securing the fiberglass container, you'll want longer screws, 5 inches or so should work.
- a single 48" x 24" (or so) sheet of whiteboard.
- Bunch of wood glue.

### Raw Materials

Because you won't be able to find individual pieces cut to the exact size, these are examples of how you can obtain the required materials in the necessary lengths.

The "remaining material" assumes the cuts are made with a 1/8 inch blade saw blade.

#### Studs

- 2x studs, cut to 60" and 33.5" (2.25" remainder)
- 2x studs, cut to 48" and 30" (17.75" remainder)
- 2x studs, cut to 48" and 48" (0 remainder - and it's ok that one is going to be slightly short)
- 2x studs, cut to 48", 24", and 24" (0 remainder. It's ok for the short side to be on one of the 24" cuts)

In total, 8x 8' studs.

#### Plywood

From a single 4'x8' sheet, you can cut it length-wise into the sizes specified.

## Plans

1. Cut studs to lengths specified
2. Create the rear-frame by joining via butt-joints the 60" studs, and 3 48" studs.
3. Attach the studs for the fiberglass container
4. Attach via butt-joints the "ribs" of the shelves to the rear-frame.
5. Attach the front "legs" as well as the rib to the frame
6. Attach the plywood to the back and the shelves.

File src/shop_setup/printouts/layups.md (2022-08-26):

# Basic Layup Procedure

<!-- This is an updated copy of the Basic Layup Procedure page, from Chapter 3, page 19 of the Cozy Mark IV plans -->

1. Preparation: Ply \#9 or Gloves (Nitrile preferred) on hands, shop temperature 75° F ± 10 °. Don't do the layup unless you know the shop will stay within this range during the entire curing time.
2. Cloth Cutting: Use the electric scissors.
  - Unless otherwise specified, cut at 45° to the fibers.
3. Surface preparation:
  - Foam: Hot-wire-cut surface needs no preparation. Sand ledges or bumps even. Fill holes or gouges with dry micro immediately prior to layup. Vacuum up the dust.
  - Glass: **Always** sand to completely dull any cured glass surface with 36 or 60 grit sandpaper. Re-sand if it has been touched with greasy fingers.
  - Metal: Dull with 220 grit sandpaper.
4. Mix Epoxy:
  - Mix for 2 minutes.
  - 80% stirring, 20% scraping sides and bottom.
  - **Hot cup: Throw it away and mix more.** A hot cup indicates exotherm.
  - Don't use a brush to stir.
  - Micro Slurry: Approximately equal volume of mixed epoxy & glass bubbles.
  - Wet Micro: Add enough bubbles for a "thick honey" mix.
  - Dry Micro: Enough bubbles so it won't run.
  - Wet Flox: Thick, but pourable mixture of mixed epoxy & flocked cotton.
  - **Applying to surface**:
    - Over foam: brush or squeegee on a **very** thin micro slurry layer. (urethane foam: Use a thick micro slurry layer).
    - Over glass: Brush on a coat of epoxy.
5. Lay on cloth:
  - Pull edges to straighten wrinkles.
  - If working alone: Roll the cloth, then unroll it onto the surface.
6. Wet Out:
  - Don't slop on excess resin; Bring epoxy up with a vertical stab of the brush (This is stippling)
  - Start in center and work out to sides.
  - *Most* of the time in a layup is spent stippling. Stipple resin up from below, or, if required, down from above.
  - **"Not wet, not white"**.
7. Squeegee:
  - If you have excess epoxy, squeegee it off to the side. Use squeegee with many light passes to move epoxy from wet areas to dry areas.
8. Preliminary Contour Fill
  - Save sanding by troweling dry micro over low areas while the glass layup is "green".
  - This is done at trailing edges, spar caps, or over any low areas.
    - The low places are overfilled with micro, then sanded smooth after full cure.
9. Knife Trim:
  - Razor-trim the edges at the "green" stage, about 3-4 hours after the layup.
  - Alternatively: Wait until a full cure, then use the variable oscillating tool to knife trim.
10. General Inspection:
  - Look for dry glass, excess epoxy, bubbles, and delamination before walking away from wet layup.
11. Cleanup:
  - Remove gloves, or rinse ply \#9 off with soap and water.
  - Epocleanse can also remove epoxy off unprotected skin areas.
  - Brushes: Rinse twice with MEK, and wash with soap and water. Throw away after 2-4 uses.

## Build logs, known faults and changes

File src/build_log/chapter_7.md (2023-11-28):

# Chapter 7 - Fuselage Exterior

In chapter 7, we take the assembled fuselage built in chapter 6, and do most of the exterior work. This is adding the air intake scoop at the rear, contouring it to have those nice, sleek curves, and glassing everything. At the end of this, the fuselage structure should be at its full strength.

## Air Intake Scoop

## Contouring Floor

One of the last things to do is to create these 1/16th inch depressions around F22, and around the landing brake. To make these, I set my calipers to 1/16th of an inch, and pressed the depth finder gauge into the foam, creating depressions that were close enough to correct. Then I sanded into the foam until the depressions were gone. These depressions only exist to enable overlap with future parts without creating a bump, so as long as they're close enough to correct, it's good enough. Highly recommend this.

Also during this, you have to tape a skirt 1 inch around the landing brake, which will be used later when we pull off the landing brake and and finish making it.

## Antennae

Because fiberglass is radio transparent, I can embed the antennae underneath the skin. Giving a slight aerodynamic improvement and a massive aesthetic improvement. With some exception, all of the antennae I'll be installing are simple dipoles, which can be made out of copper tape. The ones here, definitely so.

I spent some time on the antennae. Initially, I was thinking of placing 3 separate antennae here. A glideslope antenna, a nav antenna, and a marker beacon antenna. After discussing with people, I decided against the marker beacon, and also to combine the nav and glideslope into one. Some people also place a transponder antenna in the floor, which I decided against. I think I'll place them in the far edge of the strakes, to minimize potential interference with the other antennae.

By the way, when testing antennae layout, I highly recommend using strips of tape to do that. Much cheaper if you decide to move things around.

Once I had the antenna layout figured out, I routed a depression for the copper tape, as well as a path for the coax cable. Then I installed the copper tape, soldered up the antenna, slid some ferrites on, and potted everything.

I did not do any actual testing to check the SWR of this antenna, so the length is based off theoretical numbers - speed of light in a vacuum, with no interference. Which means this is almost certainly too long. However, even if I had used an antenna tester, the test wouldn't be valid until I finish installing the batteries and other sources of interference.

## Glassing Floor

With the antenna installed, I hade no more excuses. Time to glass the floor. The floor is intended to be 2 layers of UNI fiberglass, 60 degrees rotated from each other. One layer rotated 30 degrees one way from the centerline, the other rotated 30 degrees the other way from centerline.

I unfortunately had to glass the floor in multiple parts. After applying the first layer of glass, we ran out of epoxy hardener. We only had enough hardener to glass about a third of the second layer of glass. We peel plied everything and ordered more epoxy.

After inspecting this layup, I noticed a number of errors, and I spent quite some time sanding off fiberglass to repair this. Then I finished the glasswork... let's say more carefully. I glassed the section between the aft landing gear attach bulkhead and the firewall. Including 3 reinforcement layers over the landing gear attach point and the motor mounts. Then my wife and I did some repair work on the forward third of the fuselage. Then, my wife and I basically redid the middle half or so of the fuselage. Except we still had to do repair work on that, and then I had to repair the repairs.  Then I was finished.

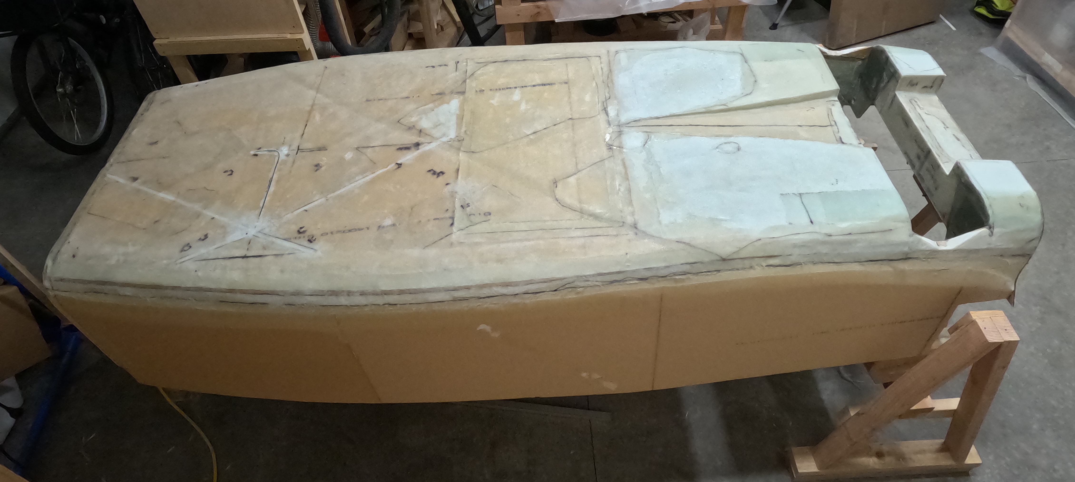
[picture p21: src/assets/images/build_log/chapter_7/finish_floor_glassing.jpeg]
finished floor glassing


<iframe width="560" height="315" src="https://www.youtube-nocookie.com/embed/mXKEVW3YBxU" title="YouTube video player" frameborder="0" allow="accelerometer; autoplay; clipboard-write; encrypted-media; gyroscope; picture-in-picture; web-share" allowfullscreen></iframe>

## fuselage sides.

With the floor glassed, the next step is to contour the fuselage sides. 

### Canard Cutout

Part one of contouring the fuselage sides is making the canard cut-out. The cut-out line vertically is at W.L. 18.9, with the top of the longerons at W.L. 23.0, that means flush with the forward face of F-28, we're supposed to cut out 2 4.1" by 6.25" squares from the longerons, foam, and the top "ears" of F-22. One on either side. I drew lines for this on the foam with pencil, then used the oscillating multitool to cut them out.

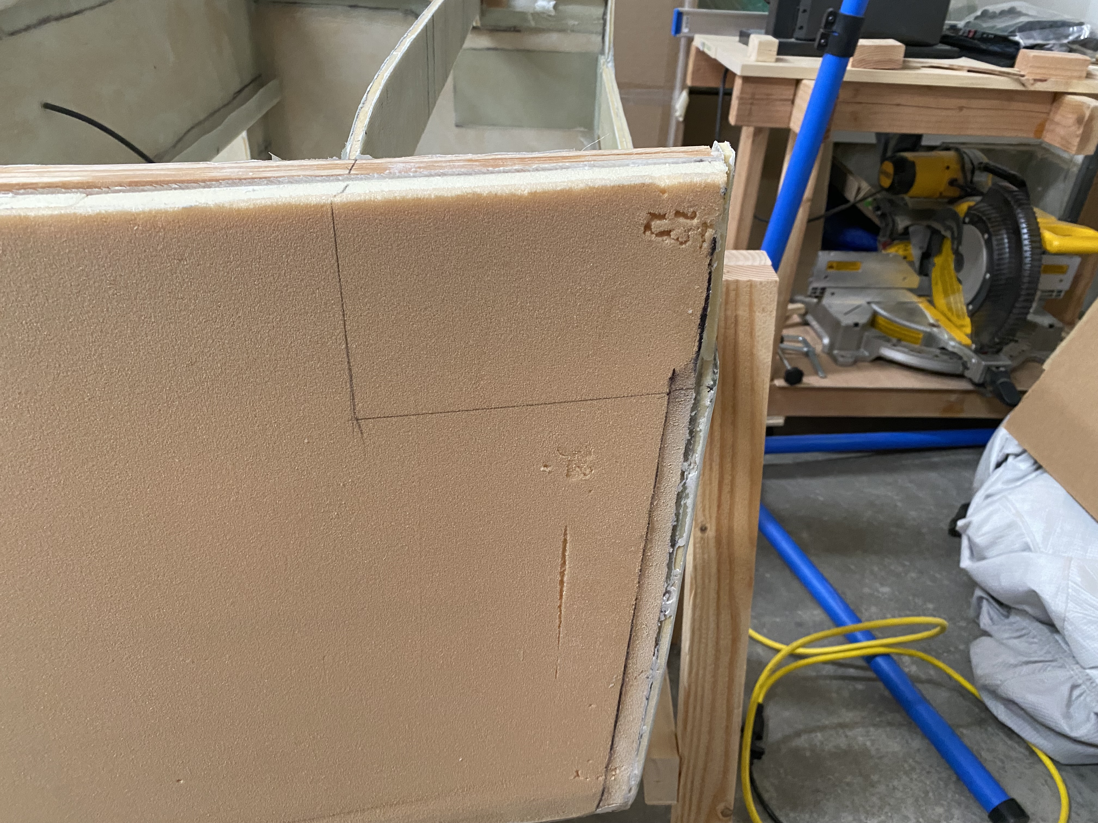
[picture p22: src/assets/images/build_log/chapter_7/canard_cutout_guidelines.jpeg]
Guide lines for the canard cutout

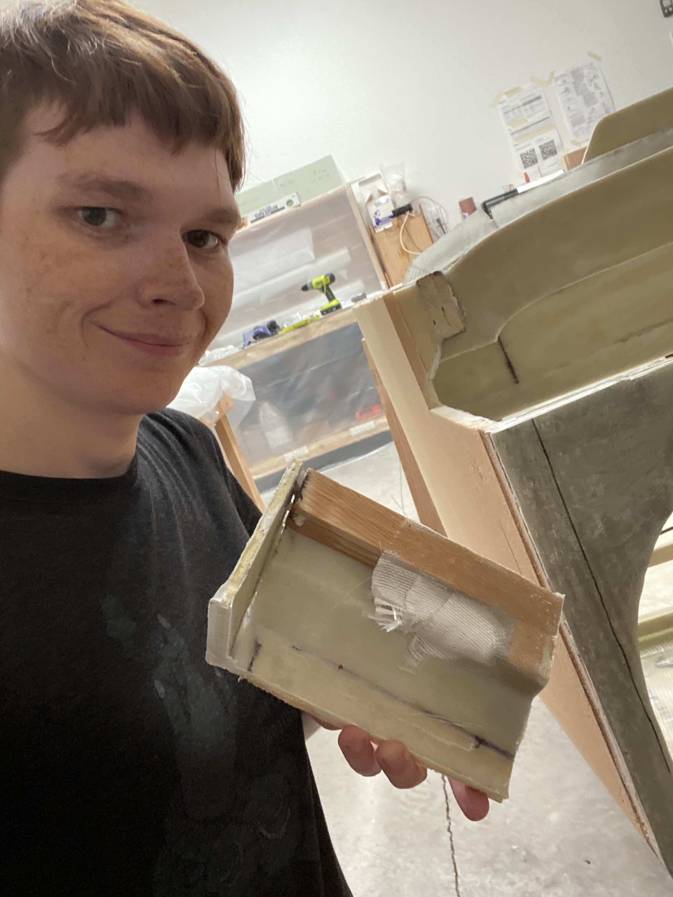
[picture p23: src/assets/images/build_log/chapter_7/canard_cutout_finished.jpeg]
Me holding the piece cut out for the canard


### Making the fuselage contour templates

Next up is making the templates for the contours. These are 4 templates that represent what the fuselage sides should look like at F-28, F.S. 33, F.S. 38, and at the firewall, with the actual contour of the fuselage smoothly transitioning between them. I printed the 4, glued sandpaper to them as sanding sticks. For the sections where I'm supposed to smoothly transition to the next, I just eye-balled it. It turned out pretty good.

Anyway, I created out the A, B, C, D templates in CAD and created the gcode for them. The next day, I actually printed them. This is because the job would take 9 hours and I'm not at all comfortable running my 3d printer overnight. I've never had an issue in the 6 years I've owned that printer, but it just feels wrong.

### Contouring the Fuselage Sides

With these printed, and the sandpaper attached, I spent a few hours sanding down the upper fuselage sides/upper longerons to the correct contour. Most of the work was done with a belt sander, but I frequently paused to check with the appropriate contour checker. Once it was close enough, I used the contour checker to finalize that sanding.

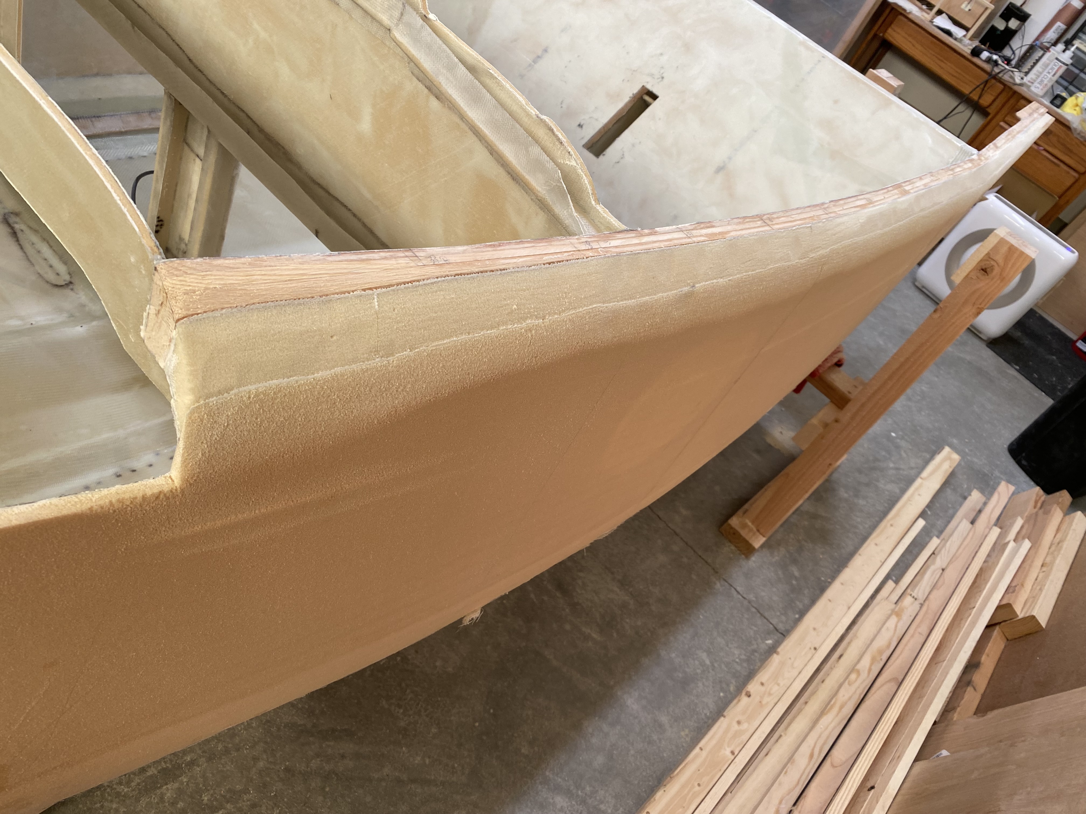
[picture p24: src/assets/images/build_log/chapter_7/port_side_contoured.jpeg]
The port-side upper longerons contoured


### Glassing the Port Side

Once the fuselage sides were contoured, I rotated the fuselage so that the port side was facing up, and I glassed that. It took me about 6 hours to do so, and thankfully I managed to get it all in one shot.

### Glassing the Starboard Side

While the port side was still curing, I prepped the fiberglass for the starboard side. I rotated the fuselage so that the starboard side was facing up, and glassed it. It took slightly less time to glass than the port side, but still close to 6 hours. This layup also came out great, thankfully.

### Finishing

While the starboard side cured, I trimmed the glass for the port side. Once the starboard side cured, I trimmed the glass on the starboard side. Once both sides were trimmed, chapter 7 was finished!

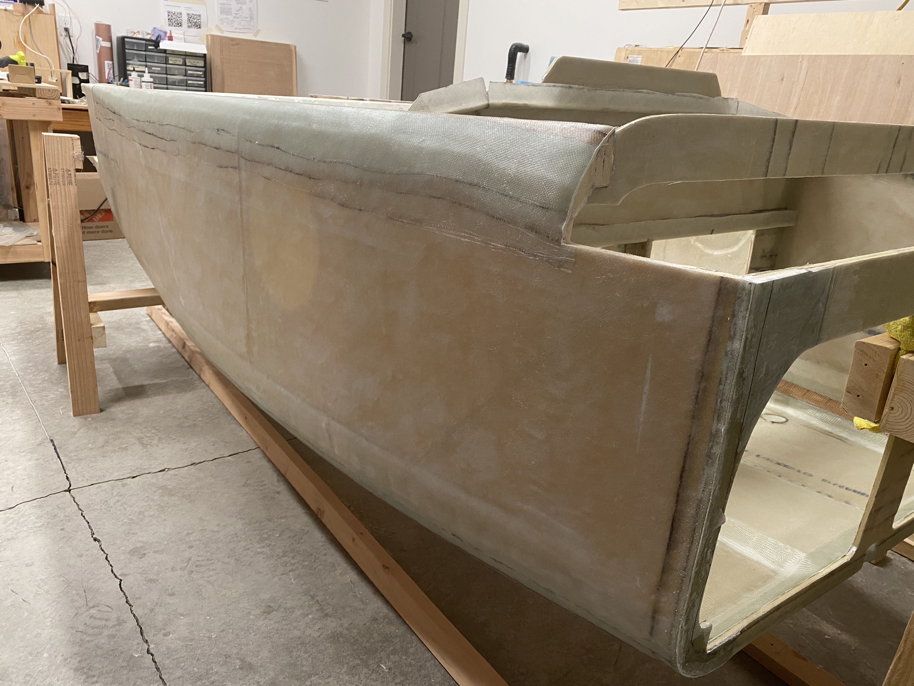
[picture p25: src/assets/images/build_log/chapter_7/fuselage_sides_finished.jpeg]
The finished starboard side


<iframe width="560" height="315" src="https://www.youtube-nocookie.com/embed/LDHFQshCZj0" title="YouTube video player" frameborder="0" allow="accelerometer; autoplay; clipboard-write; encrypted-media; gyroscope; picture-in-picture; web-share" allowfullscreen></iframe>

## Log

- 2023-04-06: Made paper template for air intake scoop.
- 2023-04-08: Traced air intake scoop template onto fuselage structure
- 2023-04-09: Installed 1" and 2" blocks of urethane foam to form basis for air intake scoop forward of the forward landing gear attach bulkhead.
- 2023-04-10: Built birch reinforcement triangles for landing gear box. Started on birch reinforcement blocks for landing gear box -> firewall.
- 2023-04-11: Attempted install of birch reinforcement blocks, but installed support blocks in incorrect locations... somehow? Would have resulted in a skewed install of reinforcement block. Spent ~2 hours removing hot glue after pulling off support blocks.
- 2023-04-14: Finished removing hot glue from aft landing gear bulkhead and lower firewall. Re-shaped support blocks such that the D parts would be level.
- 2023-04-15: Added layer of fiberglass to repair the sanded-through layers on the aft landing gear bulkhead and the lower firewall. Unfortunately, this glass was not properly wet out, and I discovered that it didn't adhere correctly and needed to be removed.
- 2023-04-16: Removed incorrectly applied fiberglass on aft landing gear bulkhead and lower firewall. Replaced with fiberglass that was pre-wetted out prior to applying to the correct surface.
- 2023-04-19(?): Installed support parts A, B, C, and D. Glassed the D parts (horizontal supports) with 2-ply BID, overlapping onto the bulkheads 1-inch. Installed urethane foam on all support parts.
- 2023-04-20: Noticed that the port-side vertical support (Part C) between aft landing gear bulkhead and lower firewall was pushed in and was not flush with the lower longerons. Removed support & urethane foam. Remade support (which I determined was quicker than sanding the support down to the wood) and re-attached it. Also re-attached new urethane foam on top of the support. Verified that everything was in the correct spot before closing up.
- 2023-04-21: Measured, cut, and fit foam panels to fill out the air intake scoop from the aft landing gear bulkhead and lower firewall.
- 2023-04-22: Installed foam panels for air intake scoop between aft landing gear bulkhead and lower firewall. Installed additional urethane foam to fill space between start of air intake scoop (as calculated) and what was previously installed.
- 2023-04-23: Built sanding block for sanding naca scoop (glued a sanding belt to a 3ft long 2x4). Applied packing tape to area forward of air intake scoop to prevent accidentally sanding through that foam. No actual sanding, though.
- 2023-04-25: Sanded urethane foam from naca scoop down to the correct shape.
- 2023-04-29: Glassed inner part of naca scoop.
- 2023-05-01: Started repair of naca scoop layup.
- 2023-05-05: Finished repair of the naca scoop layup.
- 2023-05-08: Made scans of the large M-size drawings, 3d-printed contour template for sanding the forward half of the fuselage floor to contour.
- May and June 2023: Sanding fuselage floor to contour.
- 2023-06-18, 2023-06-19: Sanded 1/16th inch depression around landing brake. Placed landing gear in place (supergluing between masking tape).
- 2023-06-21: Built up 1-inch wide "skirt" around landing brake of tape. Sanded 1/16th inch depression in forward half of fuselage floor.
- 2023-06-22: Sanded 1/16th inch depression in forward half of fuselage sides.
- 2023-06-27: Started work figuring out antennae layout. First pass: Marker beacon, 1 nav, and 1 glideslope.
- 2023-06-28: Committed to removing the marker beacon. Will also combine the nav and glideslope into a single antenna.
- 2023-07-08: Routed slots for combined nav1 and glideslope antenna. Routed slots for coax for that antenna. Cut length of coax for nav/glideslope antenna.
- 2023-07-09: Cut copper tape for nav1 and glideslope antenna. Soldered copper tapes to coax to make nav/glideslope antenna. Installed and potted antenna/glideslope antenna.
- 2023-07-10 through 2023-07-22: Prepped fuselage floor for glassing. Sanding, sanding and more sanding.
- 2023-07-17: Glassed approximately 2/3rds of fuselage floor before we ran out of epoxy hardener. Covered floor in peel ply and ordered more epoxy.
- 2023-07-20 through 2023-08-05: Sanded and prepped fiberglass to finish glassing fuselage floor.
- 2023-08-05: Glassed the aft section of the fuselage floor (between the aft landing gear attach bulkhead and the firewall).
- 2023-08-06 through 2023-08-13: Sanded and prepped fiberglass to finish glassing fuselage floor.
- 2023-08-13: Finished glassing fuselage floor.
- 2023-08-15: Repairwork for the fuselage floor.
- 2023-08-16: Finished repairing the fuselage floor.
- 2023-08-22: Released video about process of glassing the fuselage floor exterior.
- 2023-08-22: Rotate fuselage right-side up. Created canard cut-out.
- 2023-08-23: Created 3d models and gcode of the upper longeron contour checkers.
- 2023-08-24: Printed upper longeron contour checkers.
- 2023-08-25: Glued 36-grit sandpaper to upper longeron contour checkers.
- 2023-08-26: Contoured the upper longerons/fuselage sides.
- 2023-08-27 through 2023-08-29: Prepped for glassing the port side.
- 2023-08-30: Glassed the port side.
- 2023-08-31: Prep for glassing the starboard side.
- 2023-09-02: Glassed starboard side.
- 2023-09-03: Trimmed glass from port side.
- 2023-11-20: Came back later and sanded smooth the seams where the fuselage sides transition to the fuselage floor.

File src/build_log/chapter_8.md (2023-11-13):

# Chapter 8 - Shoulder Brace, Safety Belt Mount

Chapter 8, for me, is largely just installing the front safety harness attach points.

## Changes

This is simple for me. I'm only going to install the 2 front seats, so no rear harnesses nor their attach points. I'm also not installing the front step - I'll install a retractable one near the end of the build.

The only "common" plans change I made is to install the nutplates in the shoulder brace early.

Additionally, I might not be installing the rear half of the center duct?

## Shoulder Brace

The shoulder brace mounts to the top of the front seatback and contains the top mounting points for the safety harnesses. It's also where the headrests will be installed.

First, I cut out the foam cores for the shoulder brace. This is comprised of 2 pieces of 3/8th inch PVC foam that will be butted together into a corner piece. I cut these out using a box cutter knife, then I used a bandsaw to cut angles in to them so that they'd fit correctly on the front seatback. The top piece gets 4 hardpoints made of birch installed, which will anchor the shoulder straps of the safety harnesses. I installed these with 5-minute epoxy. While I was test-fitting the birch hardpoints, I broke the foam, but I repaired it with that same batch of 5-minute epoxy. One of the best things about composites is that everything is repairable. Sure, sometimes it's faster or easier to remake a part, but everything can be repaired.

Next, I joined the two pieces with finishing nails and made test fits to get it right. It took a bit of back and forth to match the contour. Later, I picked up a contour gauge which would have made this go by much quicker. But I got it to fit.

After fitting it, I pulled out the nails and joined them properly with 5-minute epoxy. In another example of how everything is repairable, after this cured, I realized that I had joined them in the wrong orientation. So I cut them apart and rejoined them in the correct orientation.

Once these were joined, I reinforced the birch with BID. I could've done this prior to joining the foam, but I didn't think to.

Next up is making some nut plates to secure the bolts that will hold the safety harnesses. These are plates of 1/16th inch thick 2024-T3 aluminum, with holes drilled to hold these nut anchors. I made some trial plates, learning how to use the tools and how to drill the holes correctly before I made the ones I'll actually be using. Once I had the aluminum drilled, I riveted the nut anchors by using a table vice to squeeze the rivets into place - the rivet squeezer I ordered hadn't arrived at that time. They're not pretty, and they wouldn't be accepted if they were, like, the wings on an rv-whatever. But, given the use case - preventing the nut anchor from rotating so that the safety harnesses can be secured - these are just fine.

With the nutplates machined, I prepped them for glassing with the recommended 220 grit sandpaper, then alumiprep and Alodine. Remember to wear a respirator when dealing with Alodine, it's pretty nasty stuff.

I drilled holes through the center of the birch+BID hardpoints, I tested the fit of the bolt, then I glassed the interior.

I used a single ply of BID and let it sit for a few hours until it was in the green stage. I floxed the nut plates in, using some blocks and quarter-inch bolts to clamp them in place, and then attached the shoulder brace in place with fresh epoxy and flox, clamping it in place with the help of 3d-printed blocks.

---

For easier to follow steps on installing the nutplates during glassing, here's what I did:

- Once the initial batch of epoxy (the one used to apply the fiberglass) is in the green stage, use a drill to open up the holes you previously drilled in the shoulder brace hardpoints.
- Apply flox (from a fresh batch of epoxy) to the nutplates where they'll meet the fiberglass.
- Place the nutplates in place, threading in a quarter-inch bolt (AN4-6) from the exterior. I also used a quarter-inch piece of wood to help spread the clamping force on the exterior foam.
- Then finish installing the shoulder brace per plans.

Once it's installed and the exterior is glassed, use a flashlight to help identify where the holes that you glassed over are. This'll make opening them up significantly easier.

---

For the exterior, I used 2 plies of BID, extending an inch over all edges. Around the upper longerons, I wasn't able to get the BID to wrap - too much complex corners - so I went back later and added some short strips of BID around there.

Additionally, all 4 shoulder harness attach points get 3 plies of UNI extending 2 inches forward of the shoulder brace, and about 3 inches around the back of the front seatback. This reverse 45 degree angle presented obvious problems with getting the fiberglass to adhere, so I printed these blocks to help clamp the fiberglass in place. Unfortunately, when I did clamped them in, I disturbed the fiberglass enough that the top layer of UNI was pulled out of place on this inner angle - which I didn't notice until after the epoxy had cured. That, with some other errors, gave me a few hours worth of sanding, plus about 45 minutes of glassing to repair this.

After repair, I opened up the holes for the shoulder brace attach bolts. First I drilled a 1/8th inch pilot hole to check I got the location right, then I widened it with a 3/16th inch bit, then finally a quarter inch bit. I got the pilot hole correct first try on 3 of the 4 attach points. For the fourth, I got it on the third try, and I filled the other 2 holes with epoxy. Finishing the shoulder brace.

## Lower Harness Attach Points

I started by cutting out 2 3 by 4 inch pieces of Finnish Birch Plywood. These are used in the outer harness attach points, to provide additional bracing against the lower longeron. By this time, I had a contour gauge, which I used to get the exact contour of the area, so I could sand the birch to fit in place. With that, I was able to get a very good fit on the first try. After that, I chamfered the front and rear edges so that the glass would smoothly transition off the birch and onto the fuselage side.

For the center harness attach area, no birth piece is needed, and instead I'll be adding fiberglass on top of the center harness attach point. This is a piece of aluminum tubing which already had 7 layers of UNI laid up on top of it. I made a paper template to figure out the dimensions needed, and cut fiberglass for the area.

Upon install, I added wet flox to fill in gaps between the birch and fuselage. Per plans, it's only necessary that the birth be flush with the lower longerons, and that it smoothly transition at the edges. Other gaps are acceptable. Then I brushed pure epoxy on the birch hardpoints and put them in place.

For laying this up, I chose to lay up all the fiberglass on plastic then transfer the layup to the install points. This is both easier and faster than trying to directly lay up on the fuselage. For the outer attach points, I made 2 rectangles with 7 layers of BID, which extend past the birch pieces by an inch. For the center piece, which had significantly more curves to deal with, I created 3 rectangles: 1 with 3 plies BID, UNI, BID, and the other 2 with 2 plies of UNI and BID. I cut these to size and individually installed them. This allowed me to better ensure that the fiberglass would conform to the curves. I didn't do this for the outer attach points, because they're significantly flatter.

After cure, I used a drill to open up the hole for the aluminum tubing in the center harness.

## Center Duct Extension

I'm not certain if I'll be using this yet. But I've started work on this, so I'll include this.

This uses a mix of old and new school techniques. First, I started work on a template for the rear electrical duct extension. Because of the curves of the fuselage floor here, the Cozy plans advise creating a template for the duct out of cardboard or scrap foam. I elected to use scrap foam for this. Next, for a transition piece from the duct through the landing gear hellhole, the cozy plans have you create a plug that transitions from square on one end to being a circle on the other end. I elected to instead 3d-print that plug, mocking it up in CAD first.

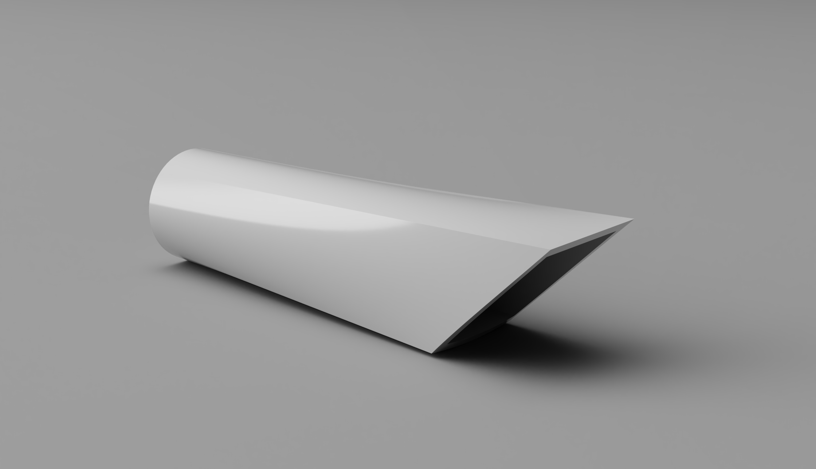
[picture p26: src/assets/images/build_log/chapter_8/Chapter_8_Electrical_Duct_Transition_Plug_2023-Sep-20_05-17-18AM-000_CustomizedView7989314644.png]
Rendered transition plug


[STL of duct transition plug](src/assets/cad/chapter_8/Duct Transition Plug.stl)

Once printed, I traced out the outline to figure out how much fiberglass to cut, and then I wrapped it in packaging tape as a cheap form of mold release.

Back to the duct itself, I used an extra piece of side wall from the front duct - I had accidentally made 2 right sides instead of a left side and a right side - to create the top, trimming it to size using my band saw.

### Will I even finish the center duct?

There's not a consensus on whether (the center duct) is structural or not. If it's not structural, then I don't see much of a point in me installing it. Except _maybe_ as a form of cable management. The center duct is meant to be a heat duct, but the electric motor won't generate enough heat for it to be worth it for me to route that heat forward. The gas builders install it because the primary output of a gas motor is heat, with only incidental amounts of usable output. So even with the (I assume) large amounts of waste in the heat duct, it's worth it to install. My plan for heating has always been more direct heat - heating pads on the seats.

## Videos

The first video I made on Chapter 8 covers the harness attach points. I had to stop because I didn't have the hardware necessary to finish them. Additionally, as I covered earlier, I'm not entirely certain if I'll even install the rear half of the center duct

Regardless, the first video covers only the harness attach points:

<iframe width="560" height="315" src="https://www.youtube.com/embed/XjEXYyxvhKU?si=UuNMbTc5CYAnUaDB" title="YouTube video player" frameborder="0" allow="accelerometer; autoplay; clipboard-write; encrypted-media; gyroscope; picture-in-picture; web-share" allowfullscreen></iframe>

## Log

- 2023-09-09: Made shoulder brace pieces, cut wood hardpoints, installed them in top shoulder brace piece using 5 minute epoxy.
- 2023-09-10: Joined shoulder brace pieces together, sanded front seatback in preparation for attaching shoulder brace to the front seatback.
- 2023-09-16: Contoured birch piece for outer seatbelt attach points.
- 2023-09-17: Installed birch & BID layup for outer seatbelt attach points. Installed layup for center seatbelt attach points.
- 2023-09-19: Started work on template for rear electrical duct extension. Created CAD duct transition piece plug.
- 2023-09-20: Printed transition piece plug. Wrapped it in packaging tape as a mold release. Finished template for rear electrical duct sides. Used an extra piece from the front duct to make the top for the rear duct.
- 2023-09-21: Cut aluminum for practice nutplates.
- 2023-09-23: Machined & Assembled practice nutplates.
- 2023-09-26: Machined & Assembled actual nutplates.
- 2023-09-30: Add first set of BID reinforcements to shoulder brace hardpoints.
- 2023-10-01: Added second set of BID reinforcements to shoulder brace hardpoints (first set didn't end up flush with the foam).
- 2023-10-04: Alumiprep'd and Alodine'd nutplates (first try). I didn't like how this came out, so I tried again later.
- 2023-10-05: Drilled center holes in shoulder brace hardpoints. Alumiprep'd and Alodine'd nutplates (second try)
- 2023-10-07: Glassed interior of shoulder brace. Installed nutplates. Installed shoulder brace onto front seatback.
- 2023-10-08: Removed clamping blocks from front seatback.
- 2023-10-09 through 2023-10-19: Sick with what was likely COVID. Be sure to take care of yourself!
- 2023-10-20: Glassed exterior of shoulder brace.
- 2023-10-21: Removed peel ply from shoulder brace. Marked spots to repair.
- 2023-10-23: Sanded fiberglass around repair spots.
- 2023-10-25: More sanding. Re-glassing the spots that needed repair.
- 2023-10-26: Opened up holes in shoulder brace hardpoints.
- 2023-11-13: Published video about Harness Attach Points

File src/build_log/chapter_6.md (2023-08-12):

# Chapter 6 - Fuselage Assembly

Rejoice! At the end of this, you'll actually have something to show to people instead of just mostly flat panels.

Now that the fuselage [bulkheads](chapter_4.md) and [sides](chapter_5.md) have been built, it's time to put them together.

Current status (Late February, 2023): Fuselage and bulkheads mostly assembled. Center keel is assembled and waiting for install. Preparing to install the floor.

## Fuselage Side Assembly

I decided to assemble my fuselage upside-down, as suggested and made popular by [Wayne Hicks](https://ez.canardaircraft.com/www.ez.org/pages/waynehicks/chapter_06.html).

I struggled a lot with building the platform to do the assembly on. It's incredibly important that this platform be level and square and I had extreme difficulty figuring out a wood structure that would suffice. My existing workbenches, which worked fine for holding the fuselage form jigs, would not work for this. I decided to purchase some T-slot aluminum extrusion and construct a work surface with that. The extrusion is machined to much higher tolerances than what I can do for wood. Additionally, for the fuselage assembly, I want to have the surface be low to the ground - my existing tables are not height-adjustable. The T-slot aluminum, while difficult to adjust the height (I can't do it with any load or surface on it), is at least possible to lower.

Once the table frame was put together & leveled, I installed the table tops. I re-used the tops from my existing tables. They're flat enough for this work - my real issue is that leveling 5 tables is incredibly hard to do. With the tops installed, including a space for the instrument panel, I used a laser level to draw a centerline across the entire table. I then drew lines marking where each bulkhead would be installed. I screwed in a piece of wood at the location where the top of the front seatback will be. Finally, I clamped a piece of wood to mark where the instrument panel should be installed.

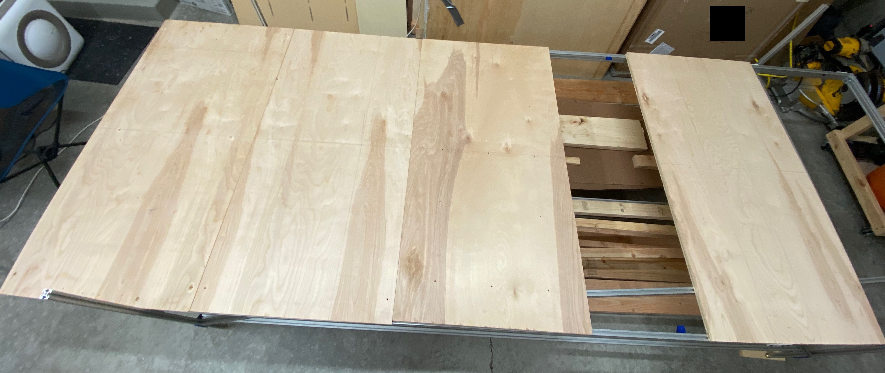
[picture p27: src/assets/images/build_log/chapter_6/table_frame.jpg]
Fuselage assembly table


### Trial Fit

With the table put together and set to the desired height, I worked on attaching the temporary firewall. First, though, I added some wood beams to stiffen it and help it keep square. I attached it to the tabletop frame using 2 m5 bolts into T-slot nuts, then screwed in a brace to keep it square with the tabletop. Once it was sufficiently attached, I tried slotting in the fuselage sides. As expected, these didn't fit. I found that a utility knife worked well to help carve out extra space from the thin and light wood I used for the temporary firewall.

Once I got both fuselage slides fully slotted in, I worked on the other end. I marked the centerline of F-22, lined that up with the centerline on the table. This allowed me to line up F-22 with the end of the fuselage sides. I found I needed to trim off material from forward end of the fuselage sides, which I did now. With that done, I drilled holes for screws to aid with re-assembling F-22, and also drew lines to mark where the fuselage sides end up when F-22 will be installed.

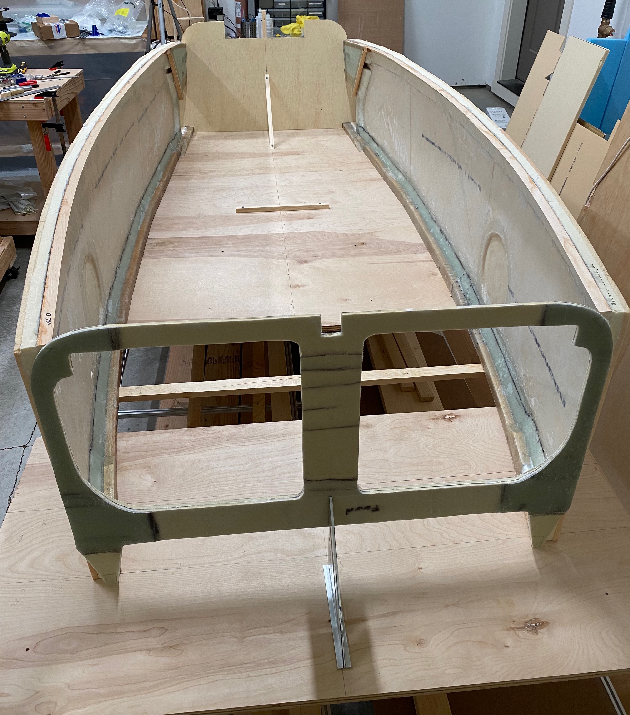
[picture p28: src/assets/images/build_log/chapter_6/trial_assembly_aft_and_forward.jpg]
Trial Assembly with sides slotted in to the firewall, and F-22 lined up with the fuselage sides


With the forward ends of the fuselage sides taken care of, I worked on getting the front seatback in place. This required me to trim some additional material from the front seatback to get it to fit. Which was disappointing, but not surprising. I tried my best to not trim more foam than necessary, but that proved impossible. In assembly, I filled the gaps with flox.

Once the front seatback was fitted, I worked on getting the instrument panel in. Which also required some trimming, but it was more around making the edges flat, and removing material from the horizontal stiffeners/cable channels. In other words, it went much quicker.

With the instrument panel fitted, I again placed F-22 on the forward end. This time, I drilled holes in the bottom longerons for screws to hold F-22 in. This provided full assurance that the bulkheads were in place. I marked on the fuselage sides where all these bulkheads would be installed, then I disassembled this and prepared for the full assembly (the next day).

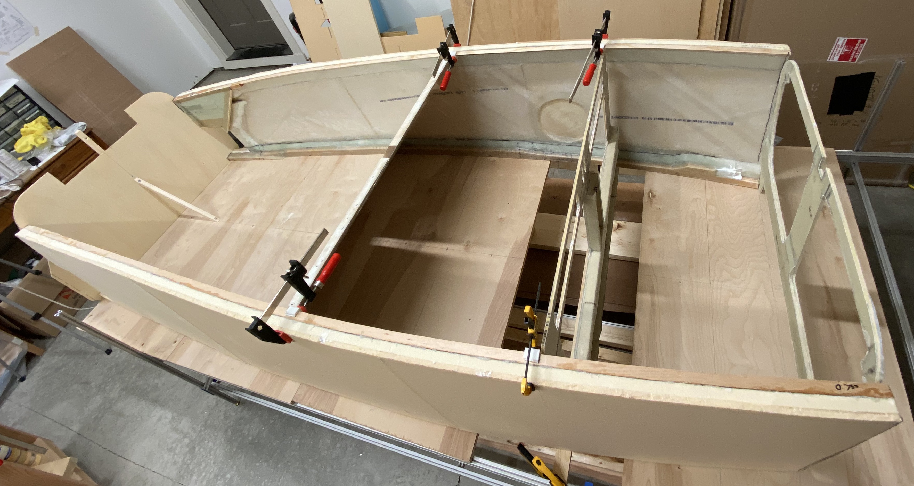
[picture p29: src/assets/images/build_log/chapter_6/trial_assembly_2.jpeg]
overhead view of the trial assembly

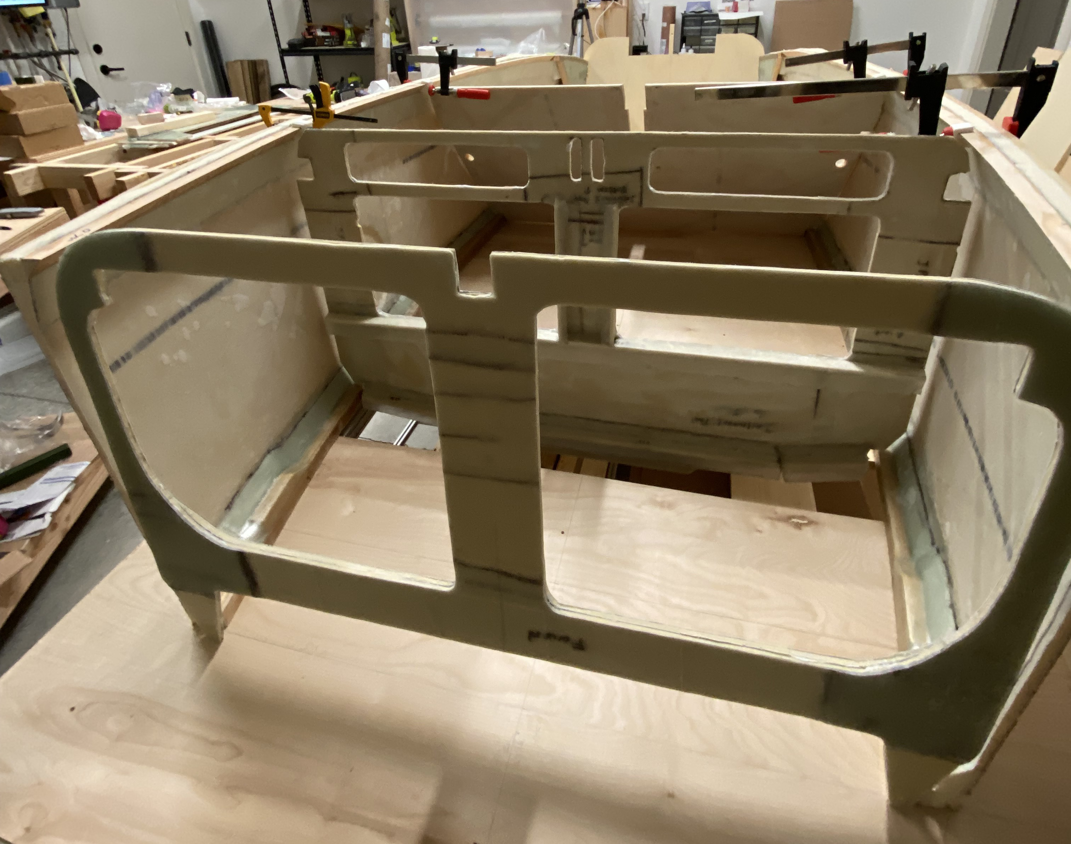
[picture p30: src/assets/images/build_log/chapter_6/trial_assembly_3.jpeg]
forward view of the trial assembly


### Actual Assembly

With the trial fit complete, now was time to start on actual assembly. I mixed up a bunch of flox (2 batches ended up being necessary - first batch used 4 oz of epoxy, the second used 2 oz of epoxy), and applied flox to the mating surfaces of the fuselage sides and the bulkheads.

I started with the front seatback: the widest bulkhead, and in some ways, the most difficult. I used some drywall anchors to hold it in. Which worked well enough, but weren't great. In hindsight, I probably shouldn't have done this. Once everything was cured, I ended up stripping one of the drywall anchors upon removal. So that's in there permanently. Thankfully, it's lightweight plastic, so I didn't take that much of a hit. I also used lengths of twine twisted taut between two pieces of wood to also clamp these together. Which worked pretty great. Probably why it's recommended by the plans.

Next up was the instrument panel. This was much easier to install, because it's just vertical. No issues. Definitely too thin to use drywall anchors, so I didn't bother.

The last of the initial bulkheads to install is F-22. F-22 fits in front of the fuselage sides, with the doubler fitting between them. I used screws to hold them in, and also more of the twine-based clamps.

I let this cure for about 36 hours, to ensure it was solid.

Once it was cured, I sanded down the flox and prepared for the reinforcement layups. These are 2-inch wide strips of 2-plies of BID. Make these using the [BID taping]({{#path_for Fiberglassing Techniques#bid-taping}}) technique. These get applied along the entire length of the seams between each bulkhead and the fuselage sides. F-22 does not get tapes to the forward side. However, it also receives 4-inch wide strips of 4-ply BID where the doubler meets the fuselage sides.

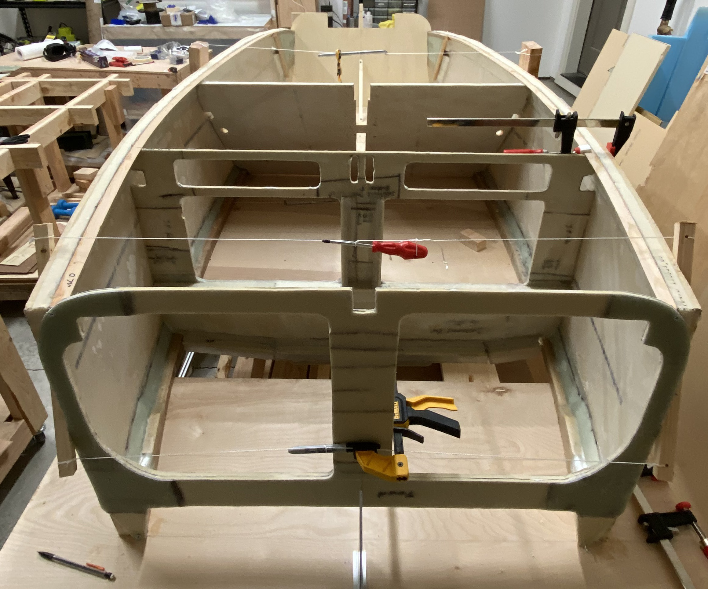
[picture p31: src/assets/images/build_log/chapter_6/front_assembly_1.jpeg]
Front assembly overhead during installation

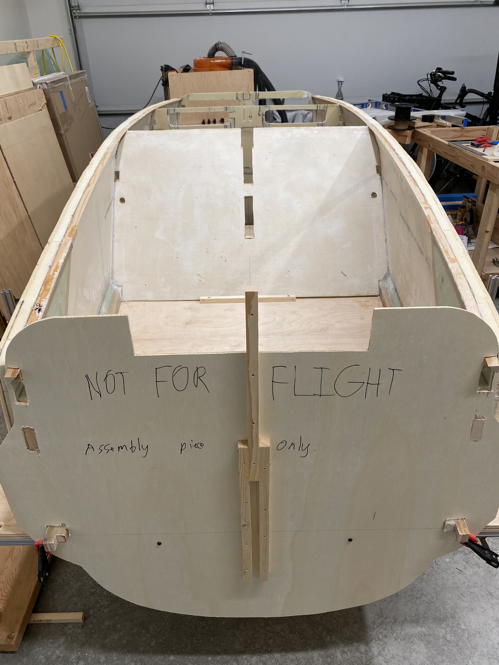
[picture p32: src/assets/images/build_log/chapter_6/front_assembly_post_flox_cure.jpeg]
Front assembly after the flox cures

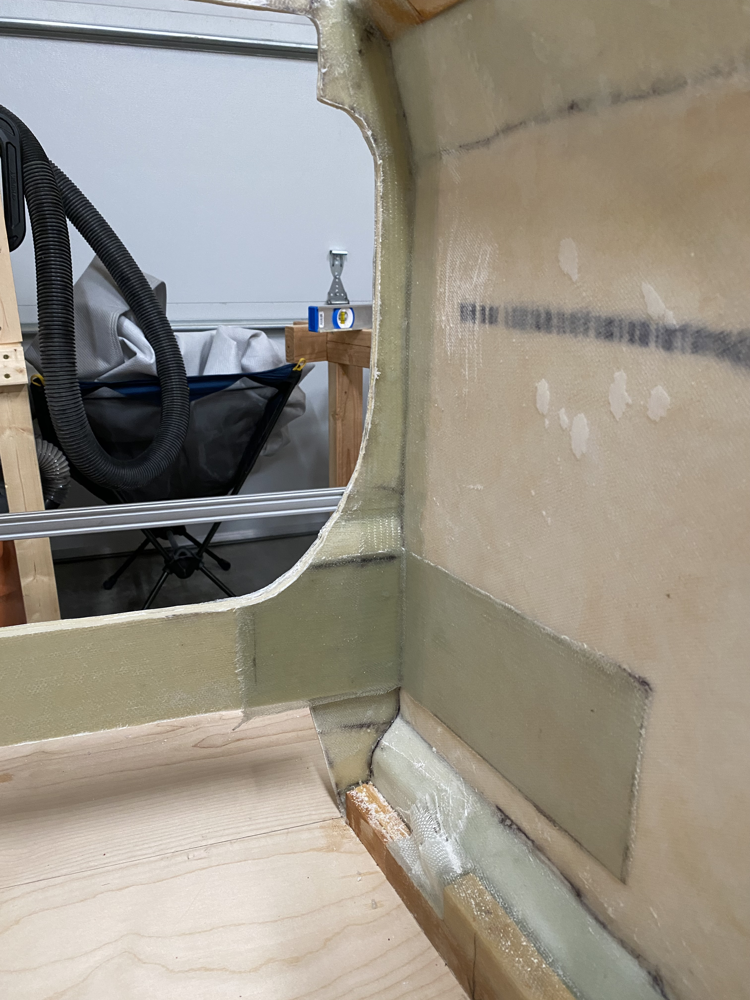
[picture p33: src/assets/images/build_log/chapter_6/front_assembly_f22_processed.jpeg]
Front assembly showing F-22 installed

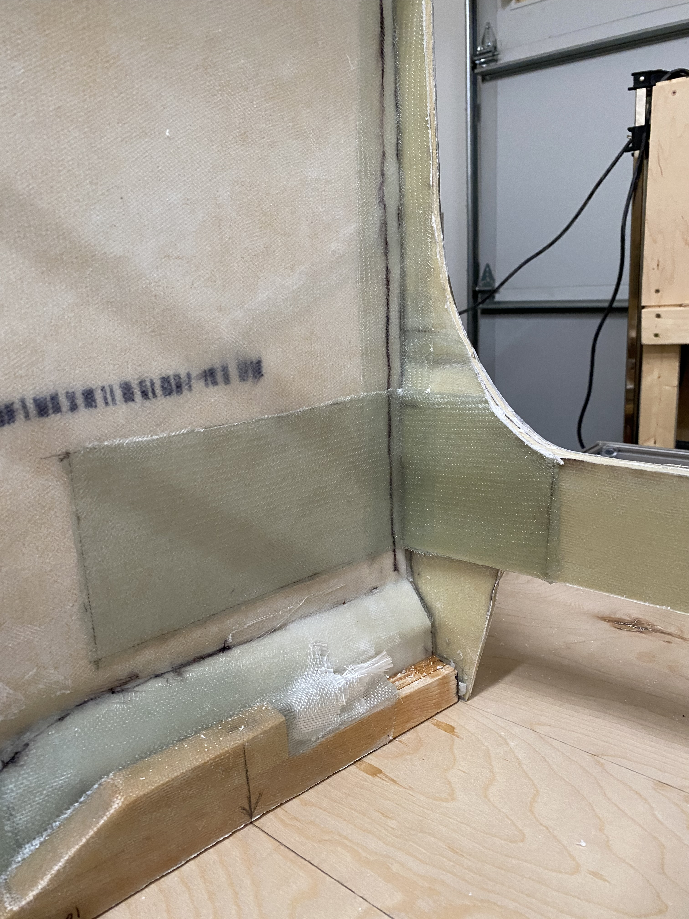
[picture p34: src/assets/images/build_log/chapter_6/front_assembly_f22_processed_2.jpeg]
Front assembly showing F-22 installed

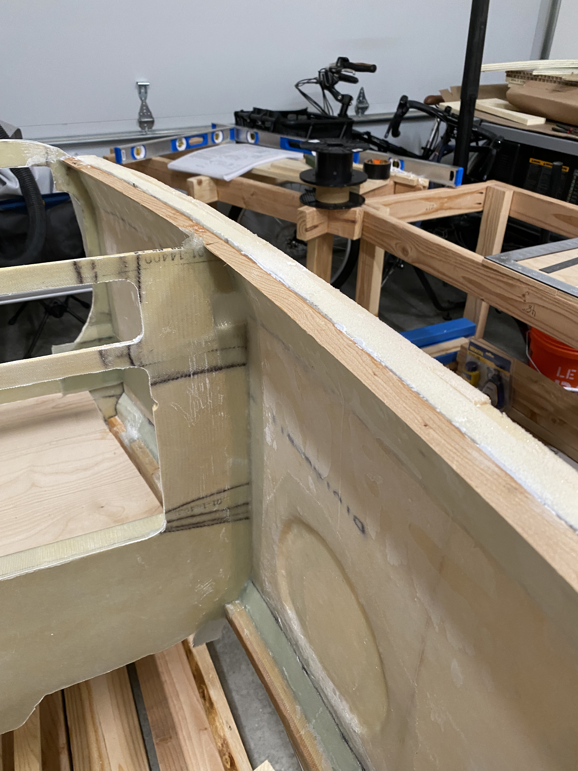
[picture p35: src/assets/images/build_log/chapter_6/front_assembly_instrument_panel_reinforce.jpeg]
Front assembly showing the instrument panel

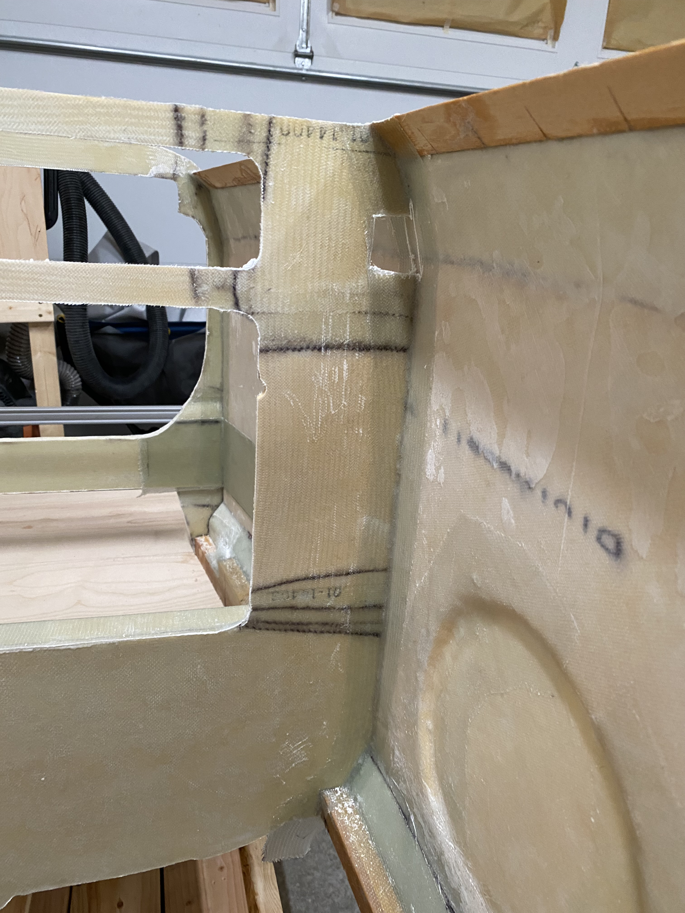
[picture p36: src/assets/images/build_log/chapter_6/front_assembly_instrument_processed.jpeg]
Front assembly showing the instrument panel

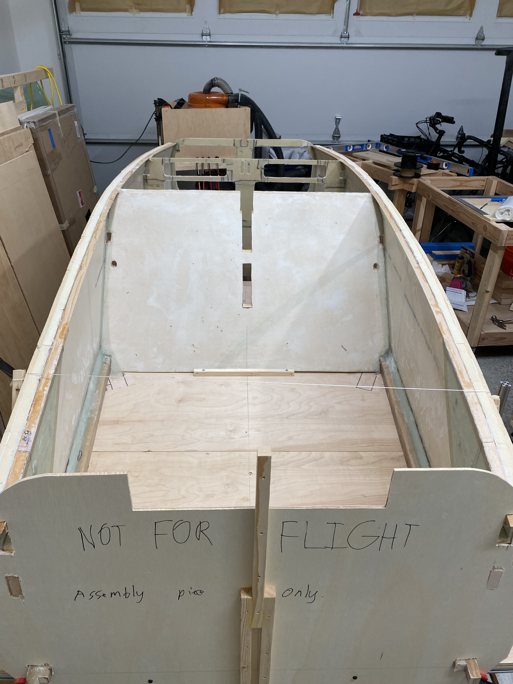
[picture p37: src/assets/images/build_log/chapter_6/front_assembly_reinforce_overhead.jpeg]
Front assembly overhead of the reinforcement layups

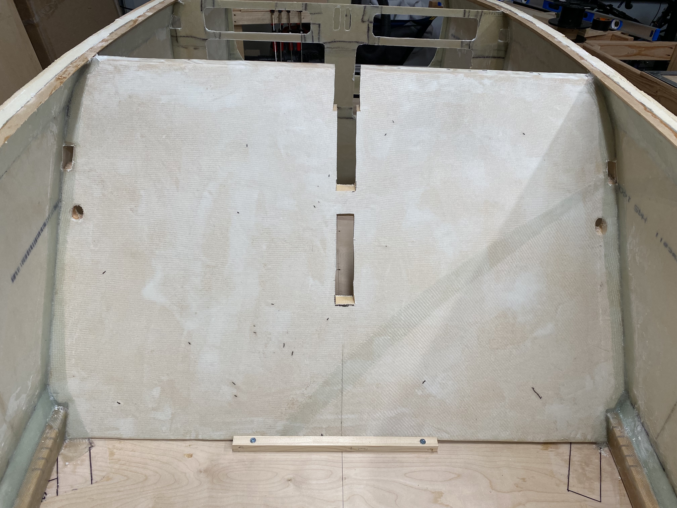
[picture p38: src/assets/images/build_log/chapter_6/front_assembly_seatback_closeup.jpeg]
Front assembly showing the aft side of the front seatback

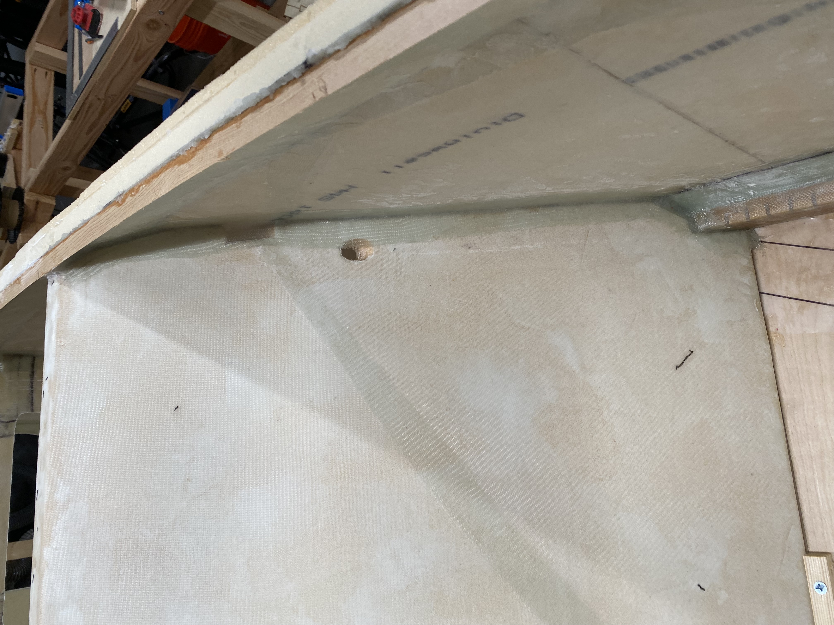
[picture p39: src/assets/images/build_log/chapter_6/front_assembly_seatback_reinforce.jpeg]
Front assembly showing the aft side of the front seatback


Once I taped as much as I could of these panels, I installed F-28. Similar to F-22, it only receives reinforcement on the aft face. That's because in the next chapter, I'll be removing foam and upper longerons immediately in front of F-28, so there's no point adding reinforcement layups there.

### Landing Gear Box

After securing as much as needed in the forward half of the fuselage, I moved aft, to the landing gear box. First, I installed the aft landing gear bulkhead. At 5 inches forward of the firewall. I had to trim it down slightly to fit, but I got it in there. After curing and adding reinforcement layups, I installed the lower part of the forward landing gear bulkhead. I hot-glued a box 8-inches long to the bulkhead, which provided exact spacing, as well as helped guide the drill so I could match-drill a 0.25 inch hole from the forward landing gear bulkhead to the aft landing gear bulkhead. This hole was drilled once the flox cured. After drilling the hole, I used a rubber mallet to knock out the wood. I then added reinforcement layups

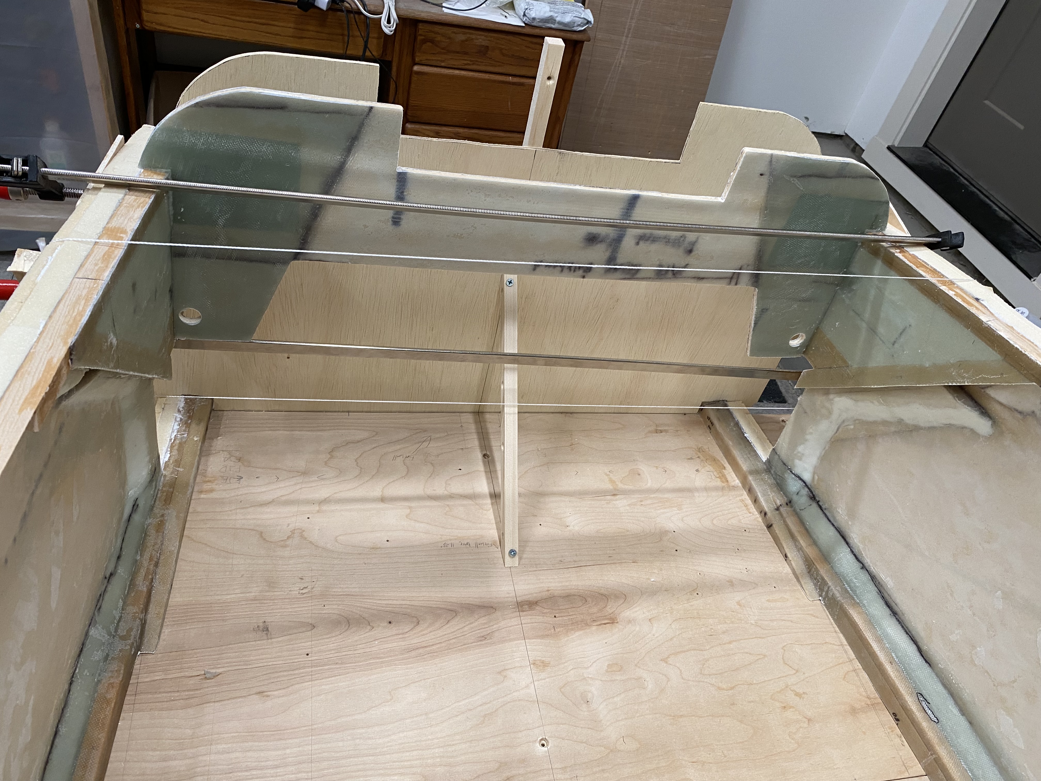
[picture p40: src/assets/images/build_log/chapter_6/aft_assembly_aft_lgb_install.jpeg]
Aft landing gear bulkhead install

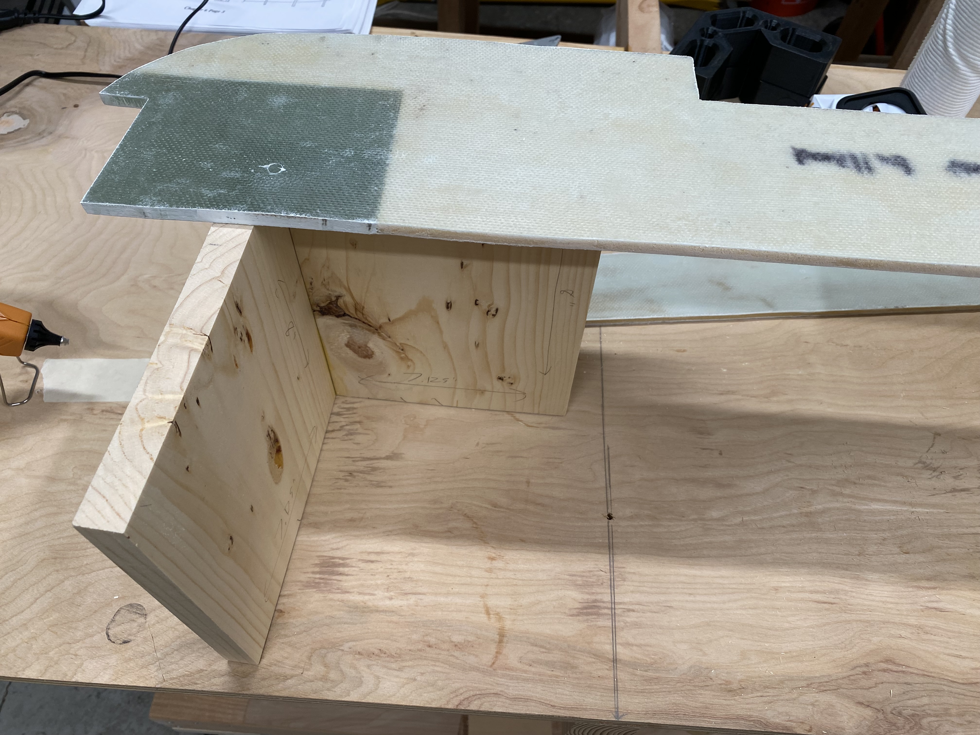
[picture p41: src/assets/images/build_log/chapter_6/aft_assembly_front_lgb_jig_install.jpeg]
forward Landing gear bulkhead jig

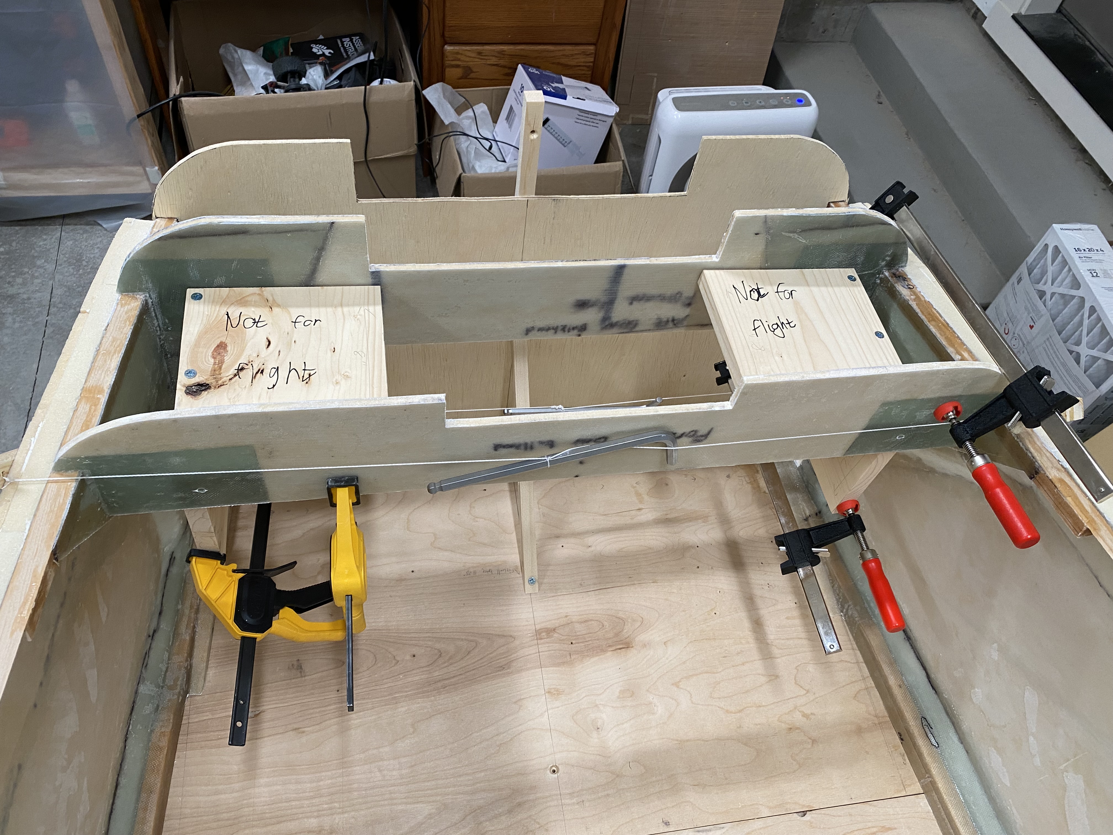
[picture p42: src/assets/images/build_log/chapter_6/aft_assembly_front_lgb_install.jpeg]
forward Landing gear bulkhead install

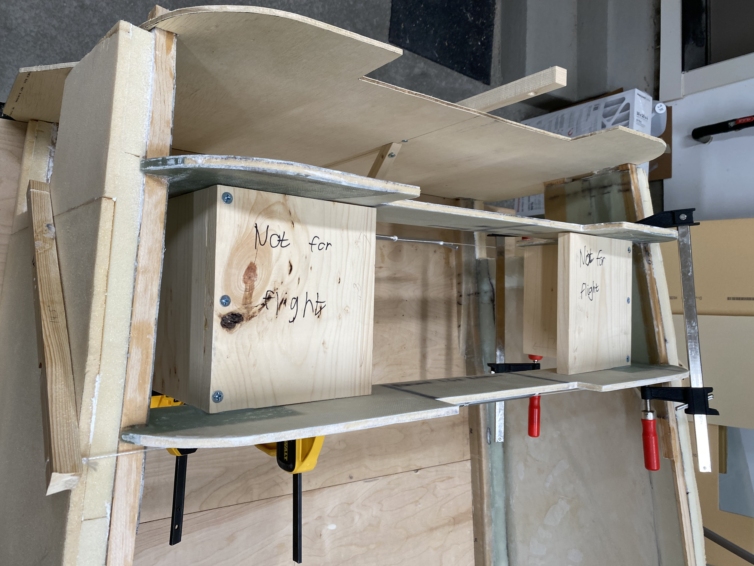
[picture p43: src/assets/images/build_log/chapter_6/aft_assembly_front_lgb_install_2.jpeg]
forward Landing gear bulkhead install


## Center Keel and Seatback Brace

The center keel adds strength to the fuselage, and contains the hot air duct (likely unused for me, but that duct is still a structural component, so I'm keeping it). It's the base of the center console and is part of the mounting point for the safety harnesses. Additionally, the fuel selector valve nominally in the center keel, but I don't need to install that, so I'm not going to work on that.

You start the center keel by first microing and glassing foam, then cutting it out. I marked the shapes in black sharpie on the foam, then I micro'd and glassed it. The triangular pieces are received 2 layers of BID, any orientation. I chose diagonal with respect to the base. The rectangular pieces received 2 layers of UNI, oriented along the length of the piece.

## The Fuselage Bottom

With the sides assembled, now it's time to install a floor.

## Log

- 2022-12-14: Started work.
- 2022-12-15 through 2022-12-16: Prepared shop for fuselage assembly - tore down the fuselage forms jig - building platform to assemble fuselage on.
- 2022-12-17: Ordered parts for constructing aluminum workbench, started work on the center keel.
- 2022-12-18: Glassed inside fiberglass parts of the center keel.
- 2023-01-08: Attached temporary firewall to assembly table. Trimmed temporary firewall to allow fuselage sides to slot in. Trimmed forward ends of fuselage sides to allow correct positioning of F-22. Installed screw holes for F-22. Started work fitting the front seatback in to the trial assembly.
- 2023-01-18: Finished trial fit of front seatback, instrument panel, and F-22 with the fuselage sides.
- 2023-01-19: Installed the front seatback, instrument panel, and F-22.
- 2023-01-21: Sanded off flox from installed bulkheads, prepared for reinforcement layups.
- 2023-01-23: Added reinforcement layups to joints between front seatback (aft joint only), instrument panel (aft side, plus below the electrical channel on the forward side), and F-22 (aft side + the 4-ply reinforcements to the doubler).
- 2023-01-24: Trimmed reinforcement layups. Prepared to install aft landing gear bulkhead.
- 2023-01-25: Installed aft landing gear bulkhead. Prepared lower part of forward landing gear bulkhead.
- 2023-01-26: Installed forward landing gear bulkhead.
- 2023-01-27: Drilled matching holes from forward landing gear bulkhead into aft landing gear bulkhead. Installed the lower piece of the permanent firewall.
- 2023-01-29: Added reinforcement layups to the landing gear attach bulkheads and F-28.
- 2023-02-01: Rotated the fuselage to be right-side-up.
- 2023-02-03: Installed the upper piece of the forward landing gear bulkhead. Added reinforcement layups to the forward side of the front seatback.
- 2023-02-04: Added layups to join the 2 parts of the forward landing gear bulkhead on the forward side. There were issues in this layup discovered after cure.
- 2023-02-07: Prepared forward landing gear bulkhead for repair.
- 2023-02-08: Moved fuselage onto sawhorses, disassembled table used for fuselage assembly.
- 2023-02-09: Added repair layups to forward landing gear bulkhead.
- 2023-02-10: Rotated fuselage back to upside-down.
- 2023-02-11: Added reinforcement/joining layups to the aft side of the forward landing gear bulkhead. Joined & glassed internal pieces of the seatback brace. Floxed them to one side of the seatback brace.
- 2023-02-12: Joined pieces for the conduit duct.
- 2023-02-13: Floxed other side of seatback brace in place. Floxed safety harness in place in the conduit duct.
- 2023-02-16: Laid up 7-ply UNI layup over the safety harness mounting point in the conduit duct.
- 2023-02-17: Glassed the outside edges of the front seatback.
- 2023-02-18: Glassed the outside of the conduit duct.
- 2023-02-20: Removed the firewall & prepared for reinstall. Joined the heat duct and the front seatback.
- 2023-02-21: Test fit center keel, determined need for an extension of the heat duct.
- 2023-02-22, 2023-02-23: Added foam as spacers for the firewall install. Sanded down to the exact length needed.
- 2023-02-24: Reinstalled firewall. It's now square. Created inside layup for the heat duct extension.
- 2023-02-25: Joined heat duct extension pieces with flox, glassed exterior.
- 2023-02-26: Installed center keel, along with heat duct extension.
- 2023-02-27: Started work on floor. Cut panels to shape, joined with 5-minute epoxy.
- 2023-03-01: Built frame to support floor during contour and layup. Cut out landing brake. Marked where contour pieces will go.
- 2023-03-02: Cut out contouring foam for floor, fit in place.
- 2023-03-04: Epoxied contouring foam for floor into place.
- 2023-03-05: Glassed ~3/4 of the floor. Stopped after running out of fiberglass.
- 2023-03-09 through 11: Sanded floor in prep for finishing glassing.
- 2023-03-12: Glassed remainder of floor.
- 2023-03-18: Installed floor onto fuselage.
- 2023-03-27: Installed BID strips on starboard side (part 1 - the strips over the lower longerons were too short)
- 2023-03-29: Installed BID strips on port side
- 2023-04-01: Installed BID strips on starboard side, finishing up the fuselage assembly.

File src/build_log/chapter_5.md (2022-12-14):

# Chapter 5 - Fuselage Sides

Chapter 4 was about making a bunch of bulkheads which are all internal to the fuselage structure. Chapter 5 involves making external parts - the fuselage sides.

In this chapter, only the interior faces of the fuselage sides will be glassed. The exterior faces will be glassed in chapter 7, when the fuselage is assembled.

Current Status: Finished! ✅ 2022-12-13

## FJ* Jigs

Status: ✅ 2022-10-30

| Template | Status |
|---|---|
| FJA | ✅ |
| FJB | ✅ |
| FJC | ✅ |
| FJD | ✅ |
| FJE | ✅ |

The FJ* jigs are used for shaping the longerons and providing a shape for the foam that will be epoxied. For the most part, these are cut from 1 by 8 (nominal) pine board. For the FJA jig, with the curve over the length of it, I chose to 3d print a template for it, which I'll use to copy onto pine board using a trim bit in my router. I also 3d printed the FJD jig, but as I was cutting FJB, I realized that it wasn't that much more effort to also create a pine version of FJD as well. Which works better because it's easier to drill in nails to wood.

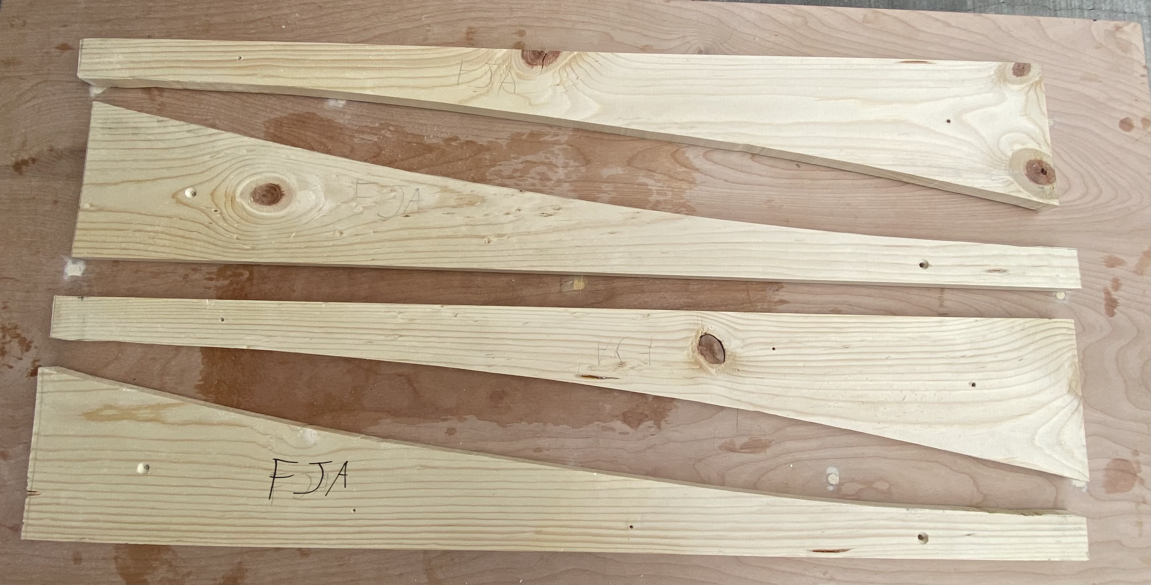
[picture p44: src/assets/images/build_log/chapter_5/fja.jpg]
Image of the 4 finished FJA jigs
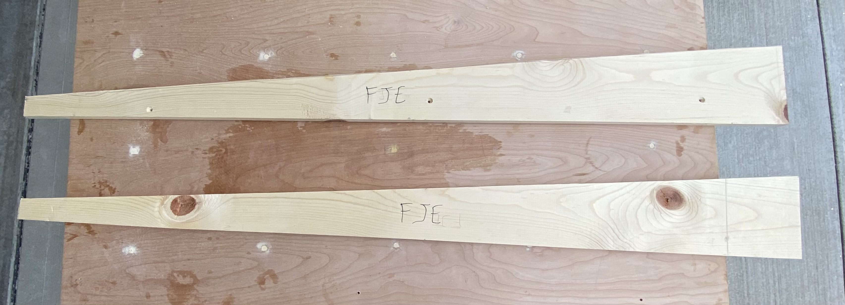
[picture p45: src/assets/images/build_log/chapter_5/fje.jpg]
Image of the 2 finished FJE jigs
 

## Fuselage Side Forms

Status: ✅ 2022-11-08

The fuselage sides need a form to rest on, otherwise they'll sag and not be the correct side. Per plans, I got a large sheet of masonite, and used it to create forms for the 2 fuselage sides. I did this by ripping it into 2x 21 inch wide by 8 foot long sheets, keeping the scrap. The scrap was used to extend the width of these sheets to the necessary 102.5 inches. Note: I accidentally cut my strips of scrap too short, by about an inch or so. I don't think it'll make that much of a difference (and if it will, I'll add on that extra inch or so of material).

Once the forms were at their full length, I aligned them on top of each other and drew out the points for the shape. Then connected the points with straight lines, then tried my best to cut it using a jigsaw. This produced two forms of the exact same shape, which I'll use to help shape the fuselage side foam.

## Upper Longerons

Status: ✅ 2022-11-08

Tips:
 - Place the forward doubler about 0.5" back from where the plans indicate. This prevents a canard placement issue that many people report.

The upper longerons (one for each side) are made of 3 long strips of 1" by 0.25" by 105" sitka spruce. Along with a stiffener and 2 doublers, also made of spruce. Because these will go on top of the foam for the fuselage sides, they need to have a slightly tighter curve than the fuselage sides. This is done by laying FJA, FJB, and FJC on their sides, with the ends of FJA and FJC being 0.5" apart, but angled so that they are adjacent by the time they meet FJB. Once you have the jigs set up, you're supposed to join the 105" spruce by painting the interiors, then use clamps & nails to hold the wood to the jigs. I was able to get away using just clamps.

Once the epoxy cured, I added the doublers and stiffeners. Per plans, I pre-drilled holes for nails on the forward doublers and the stiffeners. Then, once the wet flox was mixed up, I painted it on to the forward and aft doublers. For the center stiffeners, I found it easier to paint the flox onto the spruce strips, not the stiffeners. I also added regular flox into the saw holes, to try to counteract the fact that I made way more saw holes than I needed to. Once everything was epoxied and in place, I re-clamped everything, then added weights.

You're supposed to let this whole thing cure for at least a 24 hours. I let it cure for more than that. This is because when I initially installed the doublers, I mistakenly placed the aft doublers in the wrong orientation (I had it aligned such that the taper was aligned with the curve of the longeron. You're supposed to have that taper be facing up). I didn't realize this error until I was preparing to go to bed, ~4 hours later. I got up and re-installed the aft doublers in the correct position (and checked with the plans multiple times while I was doing so - didn't want to make an error because I was tired). Everything worked out, but it did mean that it would be way more convenient to just let it cure an additional night (and work on something else for once).

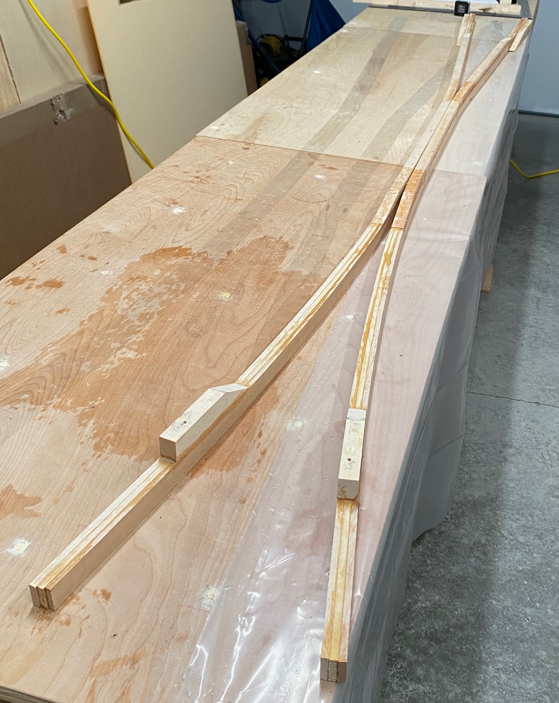
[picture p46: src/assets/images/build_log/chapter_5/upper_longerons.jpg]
Image of the completed upper longerons


## Fuselage Sides

Status: ✅ 2022-11-14

The plans state to hot glue the fuselage jigs to your workbench. Which is what I started to do, except I ran into issues both with my workbench not being sufficiently level (one of the main downsides of wanting to create a large workbench from several smaller workbenches - leveling them is nearly impossible), and with the jigs themselves having twist and otherwise not being perfectly straight. So instead, I made a series of spacers that I glued & screwed into place to keep the jigs the correct distance apart. This forms kind of the skeleton of a box, and is why I'm calling it a jig box.

Once you've done that, you're supposed to place down the fuselage forms, and nail them in place. [Per Wayne Hicks](https://ez.canardaircraft.com/www.ez.org/pages/waynehicks/chapter_05.html), you should only nail to the inside corner to ensure that the forms have entirely convex curves.

Ideally, prior to this point, you should have cut & joined your foam. Which I did not do. Instead, I placed the foam on the forms, then I used a sharpie to trace the outside curve (the non-straight edge). After, I cut the foam along traced lines, then sanded it smooth. Which worked, but was annoying. Afterwards, I then joined the foam panels together in-place on the forms. Which, again. I should have done that on a flat surface, but I didn't really have one available. It worked out, but just took longer and more effort than it should have been.

Once you have the foam put together, you're supposed to secure it directly to the forms using 5-minute epoxy. People have had issue with the foam tearing upon removal. I thought I'd be clever by applying painters tape to both the form and the foam, then applying 5-minute epoxy between the painters tape. Except the painters tape did not actually adhere to the foam. The next day, I came back and used masking tape, which worked immensely better.

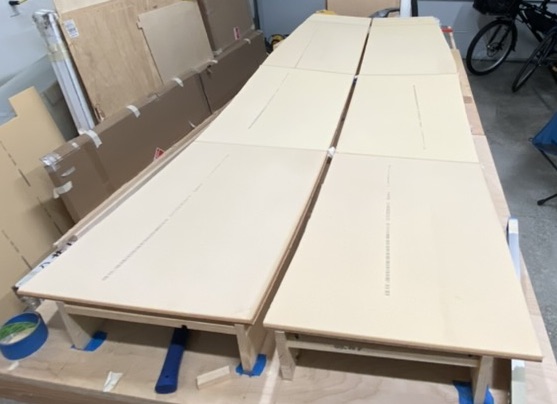
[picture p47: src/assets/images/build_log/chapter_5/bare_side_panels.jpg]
fuselage side panels with no spacers added


## Fuselage Side Spacers & Control Stick Depressions

Status: ✅ 2022-11-20

Once I had the foam secured, I started cutting the side spacers. These spacers are 3/4" low-density last-a-foam that are supposed to to be micro'd to the top, bottom and aft edges of each side panel. Unlike the high-density last-a-foam used in F-22, F-28 and the instrument panel from chapter 4, this low-density stuff cuts very easily with a utility knife.

I cut out the spacers for the top and bottom, then 3d printed jigs so I could easily cut them on my bandsaw at the angles described in the plans. Once these had been cut, I installed them to the fuselage sides with wet micro (albeit, it was on the dry side of wet micro). As per plans, I used finishing nails to help hold them down + maintain shape.

While the top and bottom spacers cured, I went about figuring out the dimensions for the aft spacers. This was mostly done by eyeballing it, along with what little precise dimensions are given by the plans. It's good enough. Again, I installed these with wet micro. While they cured, I used a router to add the depressions for the control sticks. For a gas-powered cozy, this is also where you'd create the depressions for the fuel sight gauges. I'm building an electric cozy. I don't need fuel sight gauges. While I could take off a few grams by creating these depressions, it's not going to make a difference one way or another.

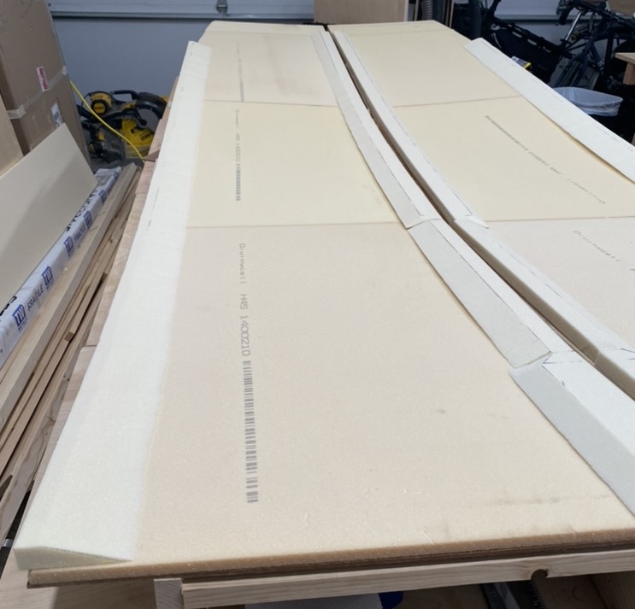
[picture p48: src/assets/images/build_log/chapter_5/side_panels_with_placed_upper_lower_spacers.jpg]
fuselage sides with shaped spacers placed on top of them

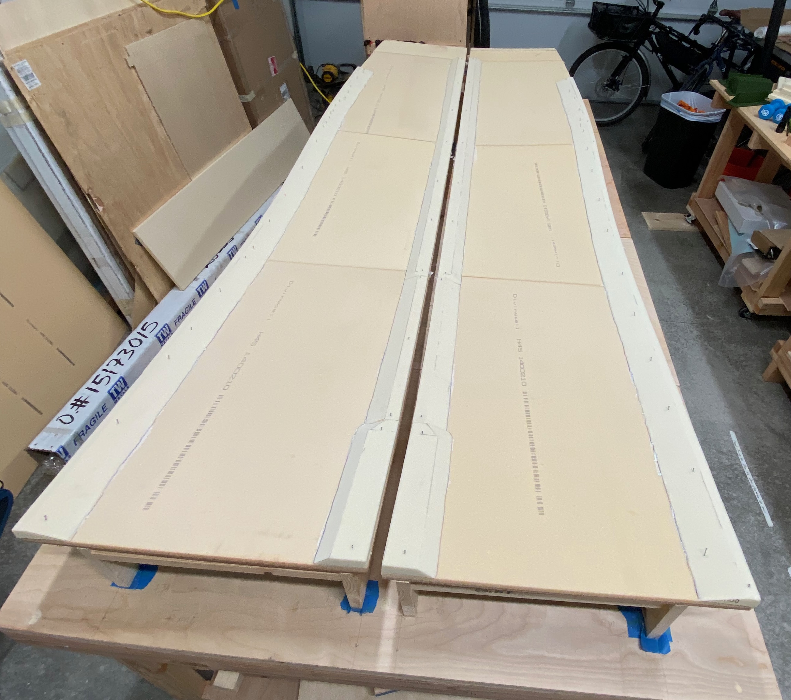
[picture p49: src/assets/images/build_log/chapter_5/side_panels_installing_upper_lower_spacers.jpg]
fuselage sides with upper and lower spacers immediately after being installed

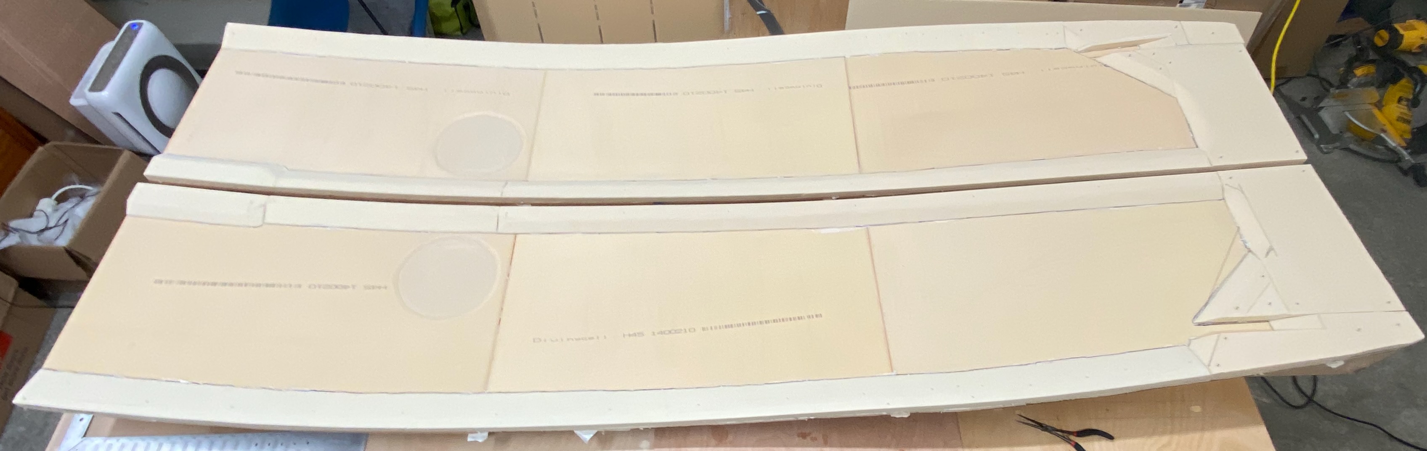
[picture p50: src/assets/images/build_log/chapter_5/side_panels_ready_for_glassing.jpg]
fuselage sides with aft spacers installed and control sticks contoured


## Fuselage Side Interior Layup

Status: ✅ 2022-11-26

The Interior Fuselage Side Layup is the first large layup you do. This is glassing the interior faces of the entire fuselage sides. It's a source of a lot of trouble for many people. I came away relatively unscathed.

A few days later after installing the spacers, my wife was available to help glass the fuselage side interiors. You could probably do this layup without any help, but her help made this immensely easier and much faster. Even with her help, this took close to 6 hours to complete. The first task was to coat all of the foam with micro, which took about 2 hours on its own. Then, with my wife's help, we laid down the UNI fiberglass on the foam. You're supposed to add 2 layers of UNI, at 30° fiber orientation from horizontal, with one layer oriented mostly forward to aft, and the other oriented in a forward-facing direction. Once the UNI was laid down, we massaged it into place. It's really important to get the fibers to conform to all of the curves and corners, which was a little bit of a pain, but we managed to do it with minimal wrinkles. Once that was wetted out, we laid down the second layer of UNI and wet it out. Again, we had some minor difficulties with handling the complex curves, but we got it. Once this layer was fully wetted out, we grabbed a flashlight and double checked the layup for any potential issues. We came across a few, but took care of them. Then, I grabbed the upper longerons, and my wife painted the mating faces with wet flox while I held them. I placed them onto the fuselage sides then clamped them down. Then, we put down peel ply everywhere, and let it sit.

After letting it cure for an hour, I pulled off the peel ply to discover the results of my work. I was very pleased with the result. Yes, there were bubbles, but they were all repairable. Most were repairable with a simple injection of epoxy, which was incredibly satisfying to do. However, a few required me to sand off the fiberglass and re-apply it. In some of these cases, I ended up sanding off too much of the foam. For those cases, I applied dry micro as a filler to get to the desired shape. In the end, I'm very happy with the results.

## Glassing the Upper Longerons

Status: Awaiting Cure

Once the fuselage side layup was finished and repaired, I moved on to glassing the upper longerons. Frankly, this was my least favorite layup I've done so far. It's a large layup, but the overall section widths were very small, as well as some vertical sections. Which meant that I couldn't really use a squeegee to spread epoxy. So I had to stipple pretty much the entire layup. I squeegeed as much as I could, to both improve the speed as well as to remove air bubbles and voids. But still, this was not a fun layup.

Because the upper longeron forward of F-28 will be getting cut off in a future chapter, I did not bother glassing forward of the forward doubler.

This layup turned out horribly. Bubbles galore and even some delaminations. Most of the issues were along the wood longerons, and only really the first 2 or 3 layers deep. Still frustrating. After spending a few days dreading this, I sanded off most of the fiberglass. This took 2 days. The day after that, I re-glassed the upper longerons. This second layup turned out significantly better - I only identified 3 issues, and then 2 more that actually looked like non-issues when I re-examined while repairing the other 3. I decided to let the epoxy finish curing for another day before repairing.

Two days after that, I performed the second repair of the upper longeron.

## The Lower Longerons

### Measuring & Marking the Lower Longerons

The plans are slightly unclear on how you're supposed to make sure the lower longerons are correctly installed. The important thing is that the lower longerons need to be installed such that each side exactly matches - each lower longeron needs to be exactly the same distance from the corresponding upper longeron. They should be close to the numbers specified in figure 5, but since it's impossible to actually get that correct (considering you're now measuring on a curved surface, when figure 5 is for a flat surface), the distances just need to be close to what figure 5 specifies. I measured the distance with a carpenter's square, using wood spacers to avoid any error from measuring a vertical distance. I recorded the distances at 10 inch intervals, and then computed their differences. After, I marked the insets on the relevant sides, where relevant. Then I prepared for glassing. Here are the values I measured, along with what figure 5 specifies:

| Distance from forward Edge (inches) | Port Side Distance (inches) | Starboard Side Distance (inches) | Difference (inches) | Value Specified in Fig. 5 (inches) |
|---|---|---|---|---|
| 0 | 20 2/16 | 20 2/16 | 0 | 20.1 |
| 10 | 20 11/16 | 20 10/16 | 1/16 | 20.6 |
| 20 | 20 15/16 | 20 14/16 | 1/16 | 20.9 |
| 30 | 20 15/16 | 21 1/16 | -2/16 | 20.9 |
| 40 | 20 13/16 | 20 13/16 | 0 | 20.9 |
| 50 | 20 14/16 | 20 14/16 | 0 | 20.85 |
| 60 | 20 14/16 | 20 12/16 | 2/16 | 20.8 |
| 70 | 20 10/16 | 20 8/16 | 2/16 | 20.5 |
| 80 | 19 12/16 | 19 13/16 | -1/16 | 20.0 |
| 90 | 18 13/16 | 18 14/16 | -1/16 | 19.0 |
| 100 | 17 9/16 | 17 14/16 | -5/16 | 17.7 |
| Aft Edge | 17 2/16 | 17 1/16 | 1/16 | 17.25 |

So, they're fairly close to each other, and relatively close to the values specified in figure 5.

### Installing the lower longerons

The plans state to add saw cuts on the inside every 4 inches, then every 2 inches where the curvature is sharper. A bunch of other builders have reported better success with doubling that - making cuts every 2 inches and every inch in sharper curves. Which I also did. Additionally, I made these cuts using a thin blade on my oscillating tool, so I feel that the more-frequent cuts will better help with this curve.

To aid with clamping the lower longerons to the fuselage sides, most builders make wood blocks with a convex inner 45° corner to match the triangular lower longeron piece. I decided that the best route for me was to instead model these jigs in CAD and 3d print them. I modeled 1 up, printed a test print to verify it works. After checking that I had the dimensions correct, I printed a bunch more of them.

The 3d-printed clamp jig, on a triangular spruce strip

In actual usage, these ended up being a bit too long, and I ended up cutting off some of the tabs with an oscillating tool. Afterwards I redesigned the jig to remove that extra tab. For those interested, there's an STL with this updated design.

CAD rendering of the updated clamp jig

- [STL of the above rendering](/assets/cad/chapter_5/lower_longeron_clamp_jig.stl)

With these clamp jigs, I installed the lower longerons. I didn't want to bother with using nails to hold the wood in place, so instead I used clamps with the clamp jigs. I didn't have enough clamps to install both triangular lower longerons at once, so I installed them on two separate days.

Installing the port-side lower longeron

After both port and starboard lower longerons were installed, I added the longeron doublers - a 20" long piece of triangular spruce which joins both lower longerons at the aft end along the hypotenuse side. I also measured and installed the LWX and LWY stringers. These are used to provide additional stability and better anchor the landing gear to the rest of the airplane.

Installing the longeron doubler and LWX and LWY stringers on the port side

### Completing the Fuselage Sides

With the lower longerons and LW\* stringers installed, the next step is to fill the area between the LW\* stringers and the lower longerons with foam, and leaving room for the electrical channel (which will be covered with 1 ply of BID). I made the channel covers using 2 molds made out of 0.75 inch low-density clark foam. I built these molds and channel covers much earlier - before I had done the first glassing of the fuselage sides. These foam pieces serve as a mold. I wrapped them in packing tape and then glassed them with 1 play of BID.  Once the stringers were in place, I installed the covers with 5-minute epoxy. Then I cut out foam to fill the area out of the same 0.75 inch low-density clark foam that I had used for the mold. I even re-used parts from the molds to fill in the area above the sloped parts of the covers. I then installed this foam with micro, and filled the voids with dry micro.

Aft end of the fuselage sides, with the stringers and electrical channel covers installed

A day later, I came back and glassed that area with 6 plies of BID. Which turned out great.

With the glasswork finished, there are 2 things left for chapter 5: Cut the fuselage sides to length, and cut out the area for the main spar.

When I measured my fuselage sides, I found that they were both too short. One measured 101.5", the other 101.???". The plans state these must be exactly 101.75", and, after panicking a bit, I checked the mailing list. According to discussion in the <a href="http://www.cozybuilders.org/mail_list/topics98/chap_05.txt" data-proofer-ignore>1998 archives page</a>, it's fine that they're short.

> Nat has in person told me twice about builders with the 101.75 a little too short and said it does not matter. Just make sure that everything is square and it will be fine.

> If you put the upper longerons where they are supposed to be and nail them as instructed all you have to do is spread the bottom a little. The jigs for the sides on the table aren't that exact. Nat told me that the long EZ sides were built flat and bent to fit so that also isn't an
exact science. He just has us build them prebent to make assembly easier.

> I talked to Nat a long time about this stuff one day and came to the conclusion that I was trying to build to tolerances that are not in
the plans and don't matter. If you have already built these things I guess that it is obvious. It wasn't obvious to me, I am new to this. That is what we pay Nat the big bucks for though. He was very gracious and helpful despite all my questions that must have seemed silly to him.

After calming down from that, I felt confident continuing. I squared off the forward end of each side, and then cut out the spaces for the main spar. Thus completing chapter 5.

Close up of aft end of completed fuselage sides, showing the space cut for the main spar
Wide shot of the completed fuselage sides

## Log

- 2022-06-05, 2022-06-06 - 3D printed FJD jigs & FJA template jig.
- 2022-09-03 - Made FJB, FJC, and FJD jigs. Made most of FJE, but need to trim a little bit more wood to get it to the final shape. Made rough cuts for what will eventually be the FJA jigs.
- 2022-09-04 - A little further progress on one of the FJA jigs.
- 2022-10-15 - Cut one of the FJA jigs to final & correct size. 3 left!
- 2022-10-29 - Ripped a 4x8 sheet of masonite into 2x 21 inch by 8 foot sheets.
- 2022-10-30 - Finished the FJ* jigs.
- 2022-11-04 - Assembled & leveled tables. Installed jigs for eventually creating the upper longerons.
- 2022-11-05 - Epoxied the 105" spruce strips together and clamped them to the jigs.
- 2022-11-06 - Shaped doublers & stiffeners. Installed them into place. Upper longerons nearly complete!
- 2022-11-08 - Unclamped upper longerons. Removed screws from stiffener. Upper longerons complete! Shaped to both fuselage side forms to the correct shape, finishing them!
- 2022-11-09 through 2022-11-13 - Constructed jig box for fuselage sides, nailed fuselage forms to the jig box, and cut and joined foam for the fuselage sides.
- 2022-11-14 - Started on the fuselage side spacers.
- 2022-11-15 - Cut out the foam that will be the upper and lower side spacers.
- 2022-11-17 - Cut to shape the upper and lower side spacers.
- 2022-11-18 - Installed the upper and lower side spacers.
- 2022-11-19 - Cut and shaped the aft side spacers.
- 2022-11-20 - Installed the aft side spacers, contoured the fuselage sides (added depressions for the control sticks)
- 2022-11-21 - Glassed the electrical channel plugs.
- 2022-11-23 - Glassed the interiors of the fuselage sides, installed the upper longerons.
- 2022-11-24 - Pulled off peel ply from the fuselage sides, inspecting the results.
- 2022-11-25 - Repaired interior layups of the fuselage sides.
- 2022-11-26 - Glassed the upper longerons - which ultimately failed.
- 2022-12-02 - Sanded off glass from failed upper longeron layup.
- 2022-12-03 - Sanded off glass from failed upper longeron layup.
- 2022-12-04 - Redid the upper longeron layup.
- 2022-12-06 - Repaired upper longeron layup (repair part 2). Added initial saw cuts through entire triangular pieces of lower longerons.
- 2022-12-07 - Some additional, final repairs of the interior fuselage side layup that I hadn't noticed until now. Additionally, measured and marked locations for lower longerons.
- 2022-12-08 - Installed the lower longeron on the port fuselage side.
- 2022-12-09 - Installed the lower longeron on the starboard fuselage side.
- 2022-12-10 - Installed the longeron doublers as well as the LWX and LWY stringers on both fuselage sides.
- 2022-12-11 - Installed electrical cover & filled area between the stringers on the lower longerons with foam.
- 2022-12-12 - Glassed the area between the LWX and LWY stringers on both fuselage sides with 6 plies of BID.
- 2022-12-13 - Trimmed fiberglass from area between LW* stringers and the lower longerons, squared off forward edges, cut out space for main spar.

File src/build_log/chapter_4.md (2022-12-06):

# Chapter 4 - Bulkheads, Instrument Panel, Front Seatback and Temporary Firewall

Chapter 4 starts off fairly simple - you're working entirely with flat shapes that are all internal to the aircraft. The only curves are the edges.

Current status: Finished! ✅ 2022-12-05

## Front Seatback

Status: Finished! ✅ 2021-10-23

The front seatback is very simple - cut down a slab of 0.75" thick foam, shape two of the edges to be 45°, and glass it. Following the advice of other builders, I used a tablesaw to make those cuts. You can see the result below.

The foam for the front seatback prior to glassing.
Angle shot of the entire foam slab prior to glassing

Closeup of the 45° edge on the front seatback foam.
Closeup of the 45 degree edge on the foam slab prior to glassing

A few days later, I did the next step, which is to add micro and UNI fiberglass to one side. I interpreted "micro" in this case to be wet micro, not micro slurry. We'll see how it turns out.

I cut out 2 lengths (approximately 42-45 inches) of full-width UNI and laid them out. I had to cut and rearrange the glass while laying it out, and there was some excess, but this worked well. Instead of using the polyester sheet as peel ply, like I had [previously]({{#path_for Chapter 3 - Education and Practice Layups}}), I used plastic sheeting. We'll see how it turns out.

The forward side of the front seatback, while curing after being glassed.
Angle shot of the front seatback after the first side is glassed

The forward side of the front seatback.
forward side of the front seatback

As you can see, it turned out fine. I did go back to using polyester peel ply for the aft side of the front seatback. Which also turned out fine and was relatively easy to pull out.

## F-28 Bulkhead

Status: Finished! ✅ 2022-07-14

The F-28 Bulkhead is a relatively small piece, and will be made of fiberglass glassed onto clark foam. I cut the foam out using a utility knife and a Fein tool.

One side turned out better than the other. The first side I glassed, I put down a significantly thicker layer of wet micro than I should have. I determined that while that wasn't enough of an issue to warrant remaking the part, and made a note to only place a thin layer of wet micro when I did the other side.

The image below is a composite image of both sides of the F-28 bulkhead, which shows the differences in the layup. Each side is labeled for convenience, both sides of F-28 received the same amount of fiberglass.

Composite image of both sides of the F-28 bulkhead.

## Instrument Panel

Status: Finished! ✅ 2022-09-18

The Instrument Panel is a little bit larger than the F-22 bulkhead. I made this by cutting pieces of it out of clark foam, and them gluing them together with 5-minute epoxy. Afterwards (much later in my case), I laid up both sides with 2 layers of BID everywhere, and then a layer of UNI running top span only.

I chose to attach and glass the stiffeners in 6 parts: First, I attached the horizontal stiffeners, which largely run across the upper span of the instrument panel. Second, I glassed the upper part of those stiffeners. Third, I glassed the lower part of those stiffeners. Which includes adding the "lip" to run wire channels and harnesses through. Fourth, I attached the vertical stiffeners, which run vertically along the center span of the instrument panel. Fifth, I glassed the inner parts of the vertical stiffeners (which don't have a lip on them). Lastly, I glassed the outer part of the vertical stiffeners. I went with this order so that the fiberglass used for the lower-horizontal stiffener would already be in place when I attached the vertical stiffeners. Additionally, I didn't want to deal with trying to add fiberglass underneath one of the "lips". For all of this glassing, I used [BID tape]({{#path_for Fiberglassing Techniques#bid-taping}}) with either 1 or 2 plies of BID, as called out in the plans.

Note: I actually ended up using UNI instead of BID for this. Which while not according to spec, I don't expect this to be an issue. I'm also expecting to make a slightly different instrument panel later on, to account for the glass cockpit I'm intending to build.

## F-22 Bulkhead

Status: Finished! ✅ 2022-11-03

Tip: When adding the doubler, be sure to apply wet micro to both sides of the doubler. Micro is supposed to applied to every side of foam that touches glass.

I had built out one F-22 bulkhead, with the aft face looking pretty decent. However, I had made a number of errors glassing the forward side. These errors were such that I'd essentially have to strip most of the fiberglass from the forward side. Additionally, after discussing this with other people, I realized that I had added way too much wet micro to the foam. With both of those, I made the decision to remake the F-22 bulkhead entirely.

For the second go around, I had ordered more clark foam to use. Which meant I could be way more liberal with material usage as this high-density clark foam is not used after this chapter. This meant that I could minimize the amount of joins I needed to make, which made things a little bit easier.

Glassing the aft face went went. It took a while before I got around to trimming the excess fiberglass. Once I did, the next day I glassed the aft face.

## Landing Gear Bulkheads

Status:

| Upper Landing Gear Bulkhead | Forward Landing Gear Bulkhead | Aft Landing Gear Bulkhead |
|---|---|---|
| Finished! ✅ 2022-11-03 | Finished! ✅ 2022-10-28 | Finished! ✅ 2022-10-30 |

The landing gear attach bulkheads are the bulkheads used to attach the main landing gear to the rest of the airplane. When installed into the fuselage in Chapter 6, they'll form a box with an open bottom. This bottom is where the mains will be inserted, and then clamped into. During installation, the forward and upper landing gear bulkheads will be joined together into one bulkhead, while the aft landing gear bulkhead will remain separated.

Note: The plans call the upper landing gear bulkhead and the forward landing gear bulkhead the same part. But they are made separately and then later joined. For that reason, as well as because "upper forward landing gear bulkhead" is a bit much, I'm going to refer to the lower portion of the forward landing gear bulkhead as the forward landing gear bulkhead. Similarly, the upper portion of the forward landing gear will be referred to as the upper landing gear bulkhead.

Tips:

1. When glassing the forward and aft bulkheads, add epoxy onto the hardpoints before adding glass. I found this significantly improves adhesion and also reduces air bubbles and other imperfections.
2. When you glass these bulkheads, it's a really good idea to apply masking tape to opposite faces. Especially around the hardpoints. I found that epoxy could very easily get underneath the foam where the bulkheads are. Masking off the underside face will likely save you from having to sand off that epoxy.

For all three of these bulkheads, I initially misread the plans and made them out of high-density clark foam like the other bulkheads are. These should be made out of lower-density PVC foam, which I am working on remaking these with. Thankfully, I had not done much other than assemble the foam core of the bulkheads. Additionally, these are still useful as templates for making additional copies of the foam cores.

When I remade them with the correct foam, I was able to cut them in one piece - no epoxying with 5-minute epoxy required.

When joined in the fuselage, the landing gear bulkheads will form a box. The fuselage struts will be bolted on in between the hardpoints on either side.

Image showing relative placement of the landing gear attach bulkheads

### Making the Hardpoints

I made  12 inch by 8 inch sheets of 22 ply BID fiberglass for the bulkhead hardpoints. Which is enough to make 8 hardpoints. Which has turned out to be a good mistake because I irreparably damaged 2 of them with my trim router while I was trying to trim them to their final shape.

Damaged forward landing gear bulkheads

Tip: If you're using a handheld router, hold the router with both hands. Don't try to hold it with one hand, and a vacuum hose (for dust collection) with the other. I was lucky and didn't get hurt when this happened.

My second attempt was much more successful. I didn't bother with the router at all, and cut the fiberglass with an oscillating tool. I used a belt sander for final shaping, and it came out quite well.

### Forward and Upper Landing Gear Bulkheads

At this point, the forward and upper landing gear bulkheads should only be glassed with 2 layers of BID and a layer of UNI (horizontally). Later in Chapter 6, the forward and upper landing gear bulkheads will be joined together with some additional reinforcement layups. In my first version of the upper landing gear bulkhead, I made the mistake of adding the reinforcement layups while building the initial part. That and other mistakes (not applying the horizontal layer of UNI to the vertical sides of the part, the 45° edges delaminated from the foam during cure) led me to conclude that I should redo the upper landing gear bulkhead. Don't make the same mistake I did, double check the layups you'll be doing before doing them.

However, my forward landing gear bulkhead was built with the 3 layers as described in the plans. Unfortunately, I rejected this part after curing both sides because I accidentally used the wrong kind of fiberglass.

---

On 2022-09-11, I discovered that some replacement BID I had switched over to in August was actually UNI. This mistake was due to blindly trusting that the BID I had ordered was actually BID, without verifying that. Once I realized this mistake, I went through my build footage to check which parts were affected, and to my relief, it was really only the forward landing gear bulkhead (the other parts I had used the not-BID for were either rejected, or were the stiffener ribs on the instrument panel, which I don't think will be an issue). I marked that part as not-for-flight, ordered new foam and fiberglass, and made a note to check that in the future the fiberglass I receive is actually I actually ordered. Once the new fiberglass came, I did verify that it was actually BID, and that the fibers were running as they should be.

---

The next forward landing gear bulkhead I made had what looked like too many air bubbles over the hardpoints. After trying to sand off enough fiberglass to repair that mistake, I realized it would be faster to just cut off the hardpoints and re-use them with a new foam core. Which is exactly what I did.

This third forward landing gear bulkhead I tried was successful. This is where I had the idea to try adding epoxy to the hardpoints before adding fiberglass, which worked amazingly well. Once both faces were glassed, cured, and trimmed, I sanded off the stray glass then drilled the quarter-inch holes into the forward bulkhead.

The finished forward landing gear attach bulkhead

(The white spots here are artifacts left over on the very top layer of epoxy from pulling off the peel ply, not indications of air bubbles. Took me a while to realize that too. It means the layup was a little too wet.)

#### Upper Landing Gear Bulkhead

The upper landing gear bulkhead is made much like the lower landing gear bulkhead. It does not have hardpoints, but it still receives the same 2-BID, 1-UNI layup.

I made a mistakes here, which I didn't discover until near the very end. The top and bottom 45° edges are not supposed to be glassed. I did glass them. Fortunately, because these edges didn't turn out evenly, decided to sand them off, with the intention to reglass them. I should've stopped once I sanded those layers off, but I also thought the faces should still be glassed, so I also sanded off some nearby fiberglass, per the instructions for doing repairs. I have since re-glassed those areas, and am awaiting curing.

Additionally, after I glassed the upper face, while removing the peel ply, I took off some of the top layer of UNI. Which isn't a big deal. Sand down the area to create a good surface for a mechanical bond, also sand the surrounding area a bit. And reglass with a layer of BID (to replace the layer of BID I damaged by sanding in to), and a layer of UNI. Just in the affected areas. Not too difficult.

The finished upper landing gear bulkhead, upper face

The finished upper landing gear bulkhead, lower face

### Aft Landing Gear Bulkhead

Unlike the forward bulkheads, the aft landing gear bulkhead does receive side reinforcement layers at this stage. Additionally, the entire bulkhead is covered in 2 layers of BID and 2 layers of horizontal UNI. The reinforcement layers for the aft bulkhead are 8 layers of UNI (vertically skewed, aligned with the inside edges) on each outer edge of the forward side, and 3 layers of UNI (vertically skewed, aligned with the inside slant) on each outer edge of the aft side. Then at the end, you drill in 2 7/8" holes near the top on the outer edges.

Forward face of the aft landing gear attach bulkhead. Aft face of the aft landing gear attach bulkhead. Side view of the aft landing gear attach bulkhead, showing off the difference in thickness between the two faces.

## Firewall

Status: Temporary firewall complete. 3 out of 4 pieces of the permanent firewall are also complete.

Temporary firewall, cut from a large 4x8 sheet of 1/8 inch birch ply I got from a big box store. It's terrible wood, but that doesn't matter because it's not going to fly. It'll be used briefly in chapter 6 as a fit check before assembling the fuselage with the lower piece of the permanent firewall.

The temporary firewall

The permanent firewall is made out of very high quality baltic birch (with a price to match).

I delayed building the permanent firewall due to worrying about the blind screws. The way you're supposed to secure the blind screws is essentially by applying a bunch of flox and hoping that the epoxy holds - has been known to cause a ton of issues, because the flox does not handle torque well. There are a couple possible solutions. One is to use hex bolts and chisel out a recess for the bolt heads. Another is to use <a href="http://www.cozygirrrl.com/clickbonds.htm" data-proofer-ignore>clickbonds from cozygirrrl</a>. A third is to wrap a metal thread around the screws. After some deliberation, I decided to go with hex bolts. I ordered a bunch of AN3-5A hex bolts from Aircraft Spruce (21/32" nominal length, 1/4" grip length, cadmium plated, undrilled), and will be finishing the firewall with them once they arrive.

After the hex bolts arrived, and not a whole lot of other excuses to put this off, I decided to start cut out the aluminum blocks for the engine mount. This was a pain, because I don't really have metal cutting tools available to me. Thankfully, aluminum can be cut with woodworking tools - it just takes a while. I cut these 4 using a dremel and my oscillating tool. This was my first time using a dremel, and I'm just happy I didn't explode a cutting wheel. If I were to build another firewall, I would 100% buy already-cut blocks of aluminum. Even if I have to oversize them, it would be worth it to me.
the aluminum motor mounts

A few days after I had cut the motor mounts, I installed them in the firewall pieces and glassed the aft faces of all 4 pieces of the permanent firewall.

About a week after glassing the aft face, I used a dremel to route out recesses for the hex bolts. I installed the hex bolts, using flox to fill out the remaining space, and then glassed the forward faces of the firewall pieces.

The next day, I pulled off the peel ply. I lined up pieces for a final "yay, I'm done" photo, when I realized I had accidentally made 2 copies of the left-middle piece.

Duplicate middle-left firewall pieces

The following day, I cut out a wood core for a right-middle firewall piece. I marked where the bolt holes should go, then I marked which face is which. Then I checked that those markings were correct. Twice. Then I glassed the aft face of that firewall piece. A few days later, I drilled out the recesses for the bolts, installed the bolts, and laid up the forward face. The next day, I pull off the peel ply and cut off the excess fiberglass. Thus completing the firewall pieces and chapter 4.

Completed firewall pieces placed next to each other

## Log

- 2021-10-09 - Cut front seatback foam panel to size.
- 2021-10-12 - [Glassed forward side of front seatback.](https://twitter.com/younata/status/1448125284012732421)
- 2021-10-15 - Cut out corners from front seatback. Glassed aft side of front seatback.
- 2021-10-23 - Finished front seatback (cut rest of holes).
- 2021-10-27 - Cut foam shapes for F-28 & the F-22 doubler (initial).
- January 2022 - Cut foam for F-22 (initial) & Instrument Panel. Glued them together. Also cut & glued the wrong foam to make the landing gear bulkheads. Didn't realize this mistake until June 2022.
- 2022-03-29 - Start cutting temporary firewall out of home depot 1/4 inch birch plywood. Which is fine, because this won't go on the final aircraft.
- 2022-03-31 - Finished temporary firewall.
- 2022-04-05 - Cut rough outline for permanent firewall.
- 2022-05-14 - Laid up 2 of 4 fiberglass bricks for landing gear bulkhead hardpoints
- 2022-05-15 - Sanded down angles of F-22 doubler to the correct shape
- 2022-05-20 - Laid up 2 more fiberglass bricks for landing gear bulkhead hardpoints. You don't necessarily need 4 bricks (you can easily get 2 hardpoints per brick. 3 if you're really careful. At the time, I thought it was 1 brick per hardpoint). But this worked out for me because I made errors cutting the 2 of the hardpoints.
- 2022-05-22 - Laid up aft side of F-22 bulkhead (initial).
- 2022-05-25 - Trimmed excess fiberglass from aft side of F-22 (initial).
- 2022-05-28 - Laid up aft side of Instrument panel and one side of F-28.
- 2022-05-29 - Laid up forward side of F-28 bulkhead
- 2022-05-30 - Cut initial hardpoints for the forward landing gear bulkhead. Router slipped from my hand and both were damaged and in a to-me unrepairable state.
- 2022-05-31 - Trimmed rest of the two larger shapes of the permanent instrument panel.
- 2022-06-03 - With help of my wife's labmates, re-cut the landing gear bulkheads. This time in the correct foam.
- 2022-07-09 - Trimmed fiberglass from aft side of Instrument Panel.
- 2022-07-10 - Re-cut hardpoints for the forward landing gear bulkhead. These ones came out much better.
- 2022-07-11 - Glassed other side of F-28.
- 2022-07-14 - Trimmed fiberglass off F-28. It's now finished!
- 2022-07-19 - Glassed forward side of Instrument Panel.
- 2022-07-28 - Cut stiffeners for instrument panel. Also cut new foam for F-22.
- 2022-07-?? - Cut out side panels for permanent firewall.
- 2022-08-03 - Drilled holes for screws in permanent firewall (side panels & bottom).
- 2022-08-04 - Sanded down hardpoints for landing gear bulkheads.
- 2022-08-06 - Attached horizontal instrument panel stiffeners with 5-minute epoxy.
- 2022-08-10 - Glassed forward side of upper landing gear bulkhead (the one without hardpoints).
- 2022-08-23 - [Pulled off pointers tape from instrument panel](https://twitter.com/younata/status/1562298805692682240). Should've done this while the epoxy was still green. There's still some small amount tape that's under some cured epoxy. Because of the location, the best I think I can do is scrape at it with a knife.
- 2022-08-24 - [Removed as much painters tape on the instrument panel as I could, time-boxing to 2 hours](https://twitter.com/younata/status/1562651689253244928). Also [cut fiberglass for glassing the stiffeners](https://twitter.com/younata/status/1562652070398038019?s=20&t=VT8aAb7IGkz6Rm5fxrwjMA).
- 2022-08-25 - Cut fiberglass in preparation for glassing the aft side of the upper landing gear bulkhead (the one without hardpoints).
- 2022-08-26 - Beveled edges of upper landing gear bulkhead. Was going to glass the aft side of this bulkhead, but ran into an issue with the new revision of the epoxy dispenser board and had to work around it.
- 2022-08-27 - Glassed the aft side of the upper landing gear bulkhead. Also glassed the upper side of the horizontal stiffeners on the instrument panel.
- 2022-08-28 - Pulled off the peel ply from the upper landing gear bulkhead & horizontal stiffeners.
- 2022-08-29 - Epoxied (with 5 minute epoxy) [the hardpoints to the forward landing gear bulkhead](https://twitter.com/younata/status/1564448840979447808). (The aft landing gear bulkhead's hardpoints still need a little bit of material trimmed from them).
- 2022-08-30 - Cut fiberglass for both fore and aft sides of the forward landing gear bulkhead.
- 2022-08-31 - Glassed one side of the forward landing gear bulkhead.
- 2022-09-01 - Glassed lower side of the horizontal stiffeners on the instrument panel. Also pulled off fiberglass from failed layup of the forward landing gear bulkhead.
- 2022-09-02 - Glassed the 45° edge on the upper end of the horizontal stretch on the aft side of the upper landing gear bulkhead.
- 2022-09-04 - Installed the vertical stiffeners on the instrument panel. Glassed the inner corners of these as well.
- 2022-09-05 - [Installed hardpoints to the aft landing gear bulkhead. Re-glassed the forward landing gear bulkhead](https://twitter.com/younata/status/1567000102744760320).
- 2022-09-06, 2022-09-08 - Cut fiberglass for the landing gear bulkheads.
- 2022-09-09 - Glassed the other side of the forward landing gear bulkhead. Glassed the exterior of the vertical stiffeners on the instrument panel.
- 2022-09-10 - Cut & shaped foam for a new upper landing gear bulkhead.
- 2022-09-11 - Realized I had accidentally been using UNI as BID, paused work as I figured out which parts were now useless and awaited for more actual BID to arrive. (Thankfully only need to redo the forward landing gear bulkhead)
- 2022-09-18 - Replacement foam for landing gear bulkhead arrived. Cut new foam for this. Also cut new hardpoint from last remaining hardpoint sheet. Also trimmed the last bit of fiberglass for the instrument panel, finishing it.
- 2022-09-22 - Glassed aft face of the forward landing gear bulkhead attempt number 2.
- 2022-09-23 - Glassed F-22 attempt number 2.
- 2022-10-02 - Glassed upper face of the upper landing gear bulkhead attempt number 2.
- 2022-10-08 - Glassed aft face of the aft landing gear bulkhead
- 2022-10-09 - Cut out and sanded foam off hardpoints from forward landing gear bulkhead attempt 2, to be used in attempt 3.
- 2022-10-12 - Rough trim of fiberglass off of the aft landing gear bulkhead. Will probably build a router table for the final trim.
- 2022-10-13 - Cut out new foam core of the forward landing gear bulkhead. Epoxied in place the hardpoints.
- 2022-10-14 - Glassed one side of the forward landing gear bulkhead.
- 2022-10-18 - Trimmed fiberglass off forward landing gear bulkhead. Did same to most of the upper landing gear bulkhead.
- 2022-10-19 - [Sanded off epoxy that got on the unglassed sides of all of the landing gear bulkheads](https://twitter.com/younata/status/1582931026292400129).
- 2022-10-22 - [Glassed the other sides of the forward landing gear bulkhead and the upper landing gear bulkhead.](https://twitter.com/younata/status/1584022751119278080)
- 2022-10-23 - Cut fiberglass in preparation for glassing the forward face of the aft landing gear bulkhead, as well as the forward face of the F-22 bulkhead.
- 2022-10-24 - Glassed the forward face of the aft landing gear bulkhead.
- 2022-10-26 - Trimmed fiberglass on the forward and upper landing gear bulkheads.
- 2022-10-27 - Sanded off fiberglass from lower 45° angled side on the lower face of the upper landing gear bulkhead.
- 2022-10-28 - Trimmed fiberglass off F-22 bulkhead. Sanded excess micro & epoxy off F-22 bulkhead. Drilled 1/4 inch holes in hardpoints of forward landing gear bulkhead, finishing the part. Sanded off fiberglass from the upper 45° angled side pieces on the lower face of the upper landing gear bulkhead.
- 2022-10-29 - Glassed the forward face of the F-22 bulkhead.
- 2022-10-30 - Finished the Aft Landing Gear Attach Bulkhead (trimmed fiberglass & drilled holes). Pulled peel ply of of the F-22 bulkhead.
- 2022-11-01 - Re-glassed parts of the lower face of the Upper Landing Gear Attach Bulkhead.
- 2022-11-02 - Re-glassed parts of the upper face of the Upper Landing Gear Attach Bulkhead.
- 2022-11-03 - Trimmed excess fiberglass from F-22 and Upper Landing Gear Attach Bulkhead.
- 2022-11-16, 2022-11-17 - Cut out the 1" by 1" by 0.25" aluminum blocks, to be used for the motor mounts on the firewall.
- 2022-11-18 - Alodined the aluminum motor mounts.
- 2022-11-21 - Glassed the aft face of the the 4 parts of the permanent firewall.
- 2022-11-28 - Installed hex bolts - a deliberate change from the plans. Glassed the forward faces of the permanent firewall.
- 2022-11-29 - Pulled off peel ply from the forward faces of the permanent firewall. Realized that I had accidentally made duplicates of the left-middle pieces in the firewall.
- 2022-11-30 - Cut new wood, marked where holes for bolts should be drilled, marked which side to glass first, and glassed the aft face of the new right-middle firewall piece.
- 2022-12-03 - Cut holes & drilled recesses for the bolts on the new right-middle firewall piece.
- 2022-12-04 - Fully installed bolts & laid up forward face of right-middle firewall piece.
- 2022-12-05 - Cut off excess fiberglass from right-middle firewall piece, completing chapter 4.

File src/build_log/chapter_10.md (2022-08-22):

# Chapter 10 - Canard Construction

## Log

- 2022-06-20: [Took delivery of wings & Canard cores](https://twitter.com/younata/status/1539030876050186240)

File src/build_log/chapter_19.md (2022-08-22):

# Chapter 19 - Wings and Ailerons

Normally, you're supposed to spend most of chapter 19 making jigs for the wings, hot-wire-cutting foam, epoxy'ing the foam together into the wing shapes, and then ultimately fiberglassing the wings. I got incredibly lucky and was able to skip all of that. In early May 2022, I reached out to Steve at Eureka CNC (Steve has since sold Eureka CNC) intending to purchase some of his cnc-cut wing cores. While he did have some wing cores available, he also offered to sell me these wings for only a few grand more. Obviously, I took the wings. A month and a half later, I took delivery of them. And they looked amazing.

Image of one of the wings, leading-edge down, resting on a foam stand

This allows me to skip approximately 3/4 of chapter 19. I'm still taking stock of exactly where I need to pick up from. I also expect to not touch this for quite some time.

## Log

- 2022-06-20: [Took delivery of wings & Canard cores](https://twitter.com/younata/status/1539030876050186240)
- 2022-07-23 & 2022-07-24: Built cart for to store wings on until I need them. [Link to tweet](https://twitter.com/younata/status/1552695879600992256)

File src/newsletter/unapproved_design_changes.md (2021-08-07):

# Unapproved Design Changes

From Cozy Newsletter \#59, copied verbatim.

We referred earlier to design changes which we haven't approved, which we think are ill-advised, and which in some cases may even be dangerous. Here are design changes to avoid:

1. Do not change the way the elevators are constructed or installed. The top surface of the elevators must be reflexed, as we show in the plans, as for example in the cross sections we show in Chapter 11, pages 5 & 6. If yours have not been built this way, scrap them and start over. A false rumor has been circulated that there is a "dead spot" in elevator response. This is not true if built according to plans, and we have proved it and can demonstrate it with our "plans-built" Cozy Mark IV. It has been reported that the same person circulating this rumor has a problem with pitch trim. This could be a symptom that there is something more seriously wrong with his airplane, if not the shape of his elevators, it could be that his canard is not set at the correct angle of incidence, and his airplane is unstable in pitch. Our flight tests apply only to a Mark IV built according to our plans. You should be aware that the fuselage is a lifting body, and the canard span and incidence needs to be adjusted for the amount of lift contributed by the fuselage. If you change the shape of the fuselage, either by making it wider, higher, or using a different canopy, or you change the angle of incidence on the main wing, there is only one way to determine whether you have a safe airplane, and that is to install a traveling 135 lb. weight, like we did, and go up to 11,000 ft. with a parachute, and determine whether the point of neutral stability is well aft of the aft c.g. limit, and whether the c.g. range is safe at the aft c.g. limit and at least 1.2 inches beyond.
2. Do not limit elevator trailing edge up (nose down) travel to 11 degrees rather than the 15 degrees we specify. If you should ever remove your vortilons, or miscalculate your c.g., or set the canard at too low an angle of incidence, or change the fuselage, and do stall tests and find the main wing start to sink at the same time the airspeed starts to fall, you will want as much nose down authority as you can muster to keep from becoming a statistic. The plans say 15 degrees trailing edge up, and that is what you should have.
3. Do not use "hard shelling" (Note: applying a mixture of micro to the foam, letting that cure, then applying glass). This results in a poorer bond between the fiberglass and the core. On airfoils, the top surface is usually in compression. A poorer bond means that the airfoil (canard or wing) skin can delaminate, buckle and fail sooner, that is, fail at a lower g-loading, than an airfoil built according to plans.
4. Do not use "tri-ax" cloth. We are not aware of any static load testing that has been done with Cozy or Long EZ wings to prove that it has as much torsional, tensile, and compressive strength as the individual layups specified by Burt Rutan, and which we use. Furthermore, it is much harder to work with because it does not conform as well to curved surfaces and can cause air bubbles (poor lamination), and it has a tendency for one or more layers to wrinkle when squeegeed, which it is not possible to correct. Also, our plans call for one less layer of glass where the ailerons will be cut out. You can't do that if you are using tri-ax. Ailerons covered with tri-ax cloth will not balance leading edge down, with the very likely possibility of "flutter" which can cause catastrophic failure of an airframe, unless you sand off at least one layer of glass, which is more work than if you had used the correct glass cloth layups in the first place.
5. Do not increase the chord length of the ailerons. There is no possible justification for doing this. It not only makes it much more difficult to balance the ailerons, but it reduces the wing cross section at the point where the bending load is the greatest. In other words it weakens your wings both in drag and in bending loads.
6. Do not increase the span of the ailerons. Our 3-place Cozy has excellent roll response. The Mark IV has even greater roll response because the 2 ft. greater wingspan puts the ailerons farther outboard which results in a greater roll moment, and also farther outboard of the downwash from the canard. There is no possible justification fo this change.
7. Do not buy "fast build" wing kits where the foam cores have been cut for wider chord and greater span ailerons, and the "kink" in the trailing edge of the wing has been eliminated. The latter changes the angle of incidence of the airfoil, which makes it different from the airplane we have tested, and causes problems in fitting the cowlings.
8. Do not eliminate the extra layups on the top of the wing which we show in Chapter 19, page 6, Fig. 32. These provide added strength to the wing where the bending and drag loads are the greatest.
9. Do not increase the span of the rudders. They are even more effective on the Mark IV than on our 3-place because of the increased wingspan. Very little rudder input is required in flying a Mark IV. Furthermore, it was discovered on the Varieze that too much rudder authority could cause a Varieze to lose control. You wouldn't want this to happen on base or on final.
10. Do not leave the lower winglets off or make them smaller. We found in our very thorough aft c. g. flight test program that the lower winglets shown in our plans give you a 0.5" c.g. safety margin protection against a main wing stall. They also provide more roll stability at slow speeds and high angles of attack. Again, something that is important on base or on final.
11. Do not eliminate the NACA scoop in the fuselage bottom and use arm pit scoops instead. The NACA scoop gives better cooling of the engine when parked nose down, and probably also in
flight. Better cooling of the carburetor or throttle body means fewer problems (if any) with hot starts. Also, if you notice, the Cozy Mark IV is quite clean underneath. We believe this (and better cowling contour) contributes to the extra 20 mph we get as compared to another aircraft with arm pit scoops, fixed gear and the same horsepower.
12. Do not cover the top of the canopy. The compliment we receive most often on the Cozy and Cozy Mark IV is its wonderful visibility. If we had gull-wing doors, we couldn't have a full bubble, but with a side-hinged canopy it is a wonderful feature. Install the full bubble first. Then, if sun bothers you (it helps to keep you warm at high altitudes in the winter), you can always wear a baseball cap. Then, if you are still bothered by the sun, you could use cling-type plastic shades, which are moveable, over your head. If you really like reduced visibility, you can always paint part of the bubble. The latest pictures we have seen of the Velocity show that they removed most of the cover over the top of their canopy. We consider this to be a safety consideration.
13. Do not hook your fuel tanks together. Having two separate tanks is a safety feature. If you lose one fuel cap with both tanks hooked together, all of your fuel will be siphoned out, and you will become a statistic.
14. Do not eliminate the sumps under each tank. They make all of your fuel usable, and allow you to fly for a little while after the gauge shows empty. Although not recommended, you can run one tank completely dry, switch, and keep on trucking. We have done this (accidentally) twice in the last 12 years.
15. Do not locate your fuel selector valve remotely. Experience with the Varieze was that the remote location of the fuel valve was the cause for more than one emergency landing.
16. Do not buy components from custom shops without calling us first. Custom shops are in business to make money. They may use unskilled labor and take shortcuts, and sometimes their parts don't fit or are unairworthy. They will probably claim their parts are better, but then ask you to sign a waiver relieving them of any product responsibility or liability, and will not guarantee the airworthiness of parts they supply. We have heard of some very bad experiences some builders have had with custom shops. If you are not willing to build the parts yourself per plans, you would be better advised to build a Velocity. The Swings have a pretty good record.
17. Do not install retractable main gear. Our airplane was not designed for it. Most people agree the benefit (if any) isn't worth the cost (and we aren't just talking about dollars).
18. Do not change the size or shape of the engine cowlings (in other words, use the cowlings we approved from Feather Lite). Our cowlings were contoured to have nice clean airflow back to the prop, to avoid a vacuum or reverse airflow at the prop. It was interesting to hear that one 4-place canard aircraft (we won't mention the name), which has been highly advertised, and which has a very blunt rear end, has not yet been able to meet its performance goals of useful load and speed because it cannot generate enough thrust after becoming airborne. We suspect that it is because the prop is spinning in reverse airflow or a vacuum (you know, like behind a semi).

[A bunch of text to backup that unapproved design changes tend to have bad results]

Lastly, if you do not build your airplane according to plans, the Cozy Mark IV Owner's Manual does not apply, and we ask that you not register or insure it as a Cozy Mark IV!

---

Which is why I'm not building a Cozy Mark IV, I'm building a Coz-E, which happens to be largely similar to the Mark IV, but is not the same airplane.

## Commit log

2021-07-27 I built a workbench
    [workbench.f3d]
2021-09-04 Add some printouts and other good information to have in the shop
    [dowel_mount.stl]
2021-12-24 Notes on the current state of chapter 4
2022-03-27 Update on current status of chapter 4
    [Workbench_v1.4.f3d, workbench_v1.0.f3d]
2022-03-27 lowercase asset names
    [workbench_v1.4.f3d]
2022-03-27 More notes on current status
2022-04-24 I changed workbench v1.4 before building it, update instructions to reflect the new plan.
    Clarify instructions for the workdesk
    [workbench_v1.0.f3d, workbench_v1.4.f3d]
2022-04-26 I assembled a top frame for another workbench
2022-04-27 Images of the work desk frame being assembled
2022-05-16 I have heating in the garage now.
2022-05-24 Update with current status of chapter 4
2022-05-24 Current state of the epoxy dispenser is that both tubing materials I've used are permeable to the epoxy hardener. Which makes me sad.
2022-06-28 I bought some wings
2022-08-22 Add dated log entries
    After discussing with a friend on logs in experimental aircraft (and
    how poor the logs are for most experimental aircraft), I have decided
    to do my small part improving that.
    In addition to the more prose-y version of what was done, I also have
    a list of what work was done, along with when that work happened.
    In that vein, this also creates pages for chapter 5 (I started
    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
2022-08-28 Glassed the aft side of the forward upper landing gear bulkhead
2022-10-10 Update with work for the past couple weeks.
    Give a consistent naming to the upper and forward landing gear bulkheads
2022-10-29 Finished the forward landing gear bulkhead
2022-10-29 Update current overall status of chapter 4.
2022-10-29 I started work no the fuselage side forms
2022-11-04 Finished F-22 and the upper landing gear attach bulkhead
2022-11-09 Finished the upper longerons and fuselage side forms
2022-11-14 Spent the past week on the fuselage side foam
2022-11-23 AN4-6A bolts are too large for the firewall
2022-12-08 Update the current status of chapter 4
2022-12-09 Installed the port side bottom longeron
    [lower_longeron_clamp_jig.stl]
2023-01-09 Finally unblocked and working on the fuselage again
2023-11-13 Chapter 8 details
    [Duct Transition Plug.stl]
